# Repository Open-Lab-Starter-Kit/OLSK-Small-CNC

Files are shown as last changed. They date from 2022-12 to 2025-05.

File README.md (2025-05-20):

<div align="center"><h1 style=align="center">OLSK Small CNC V3</h1></div>

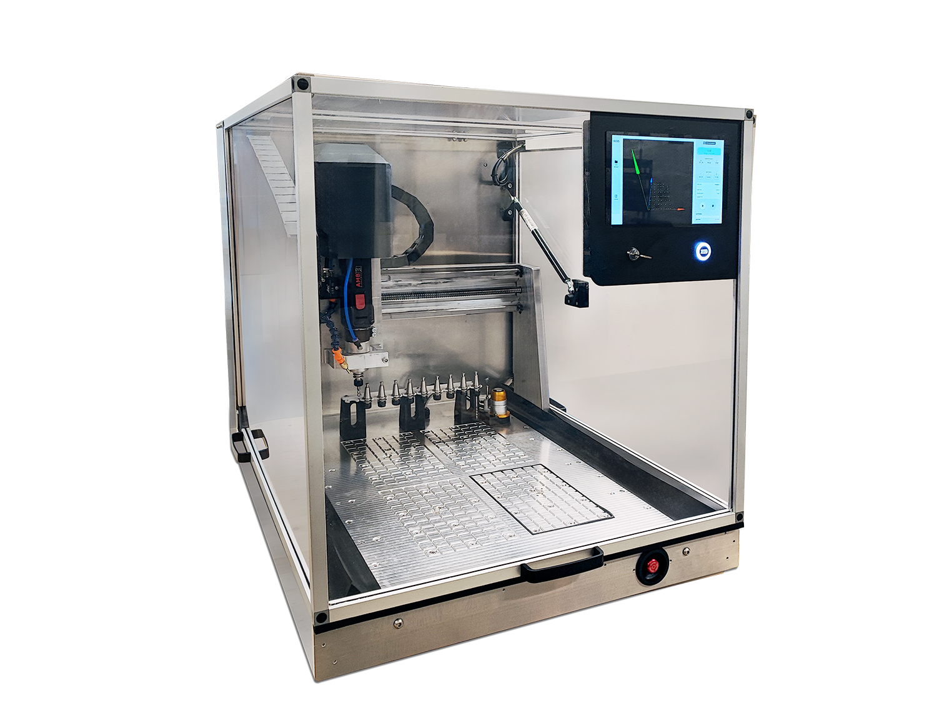
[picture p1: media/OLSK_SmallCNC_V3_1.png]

<div align="center"><i>Open Source CNC Milling machine - Small version - Open Lab Starter Kit</i></div>

<br>

Introduction
--

The OLSK Small CNC V3 is a desktop CNC milling machine with an innovative open-source tool changer, one of the first in an open-source machine.



The Assembly Manual
--

All OLSK machines are open source and have the BOM and necessary files available in this repository for replication. The assembly of parts is also documented in a workbook where each step contains a list of parts, tools and instruction remarks, following a logical order to provide a smooth assembly.

- **[Assembly Manual](https://open-lab-starter-kit.github.io/OLSK-Small-CNC/)**

Specifications V3
--

- machine external dimensions: W740mm x D960mm x H800mm (~H1600mm open door)
- working area: 400mm x 600mm x 150mm Width(X) x Depth(Y) x Height(Z)
- Automatic tool changer (capacity: 10 tools)
- Automatic tool measurement
- Automatic tool cleaning
- Coolant System
- Integrated liftable full-enclosed housing
- Flush-mounted 24V emergency stop
- Key Operated
- Universal bed (fixture clamping and vacuum)
- Closed Loop DC Servo Motors
- Belt decoupling on all axes
- Mounted touch screen
- Software: OLOS

Files
--

- **[CAD](cad)**
- **[Firmware](firmware)**
- **[Settings](settings)**
- **[BOM](OLSK_Small_CNC_V3-BOM.xlsx)**
- **[Wiring Schematic](OLSK_Small_CNC_V3_WiringSchematic.pdf)**

Author
--

OLSK Small CNC has been designed and built by **[InMachines Ingrassia GmbH](https://www.inmachines.net/)**.



<be>

Machine design:
- **[Daniele Ingrassia](https://www.linkedin.com/in/danieleingrassia/)**

PCB Design:
- **[Wilhelm Schütze](http://fabacademy.org/archives/2015/sa/students/schutze.wilhelm/index.html)**

The machine is part of the **[Open Lab Starter Kit (OLSK)](https://www.inmachines.net/open-lab-starter-kit)** group of open source digital fabrication machines.

OLSK is developed by **[InMachines Ingrassia GmbH](https://www.inmachines.net/)** for the **[Dtec project](https://dtecbw.de/home/forschung/hsu/projekt-fabcity)** at **[Fab City Hamburg](https://www.fabcity.hamburg/en/)**.

OLSK Partners:
<br><br>


Contact
--

- daniele@inmachines.net
- [https://www.inmachines.net/](https://www.inmachines.net/)

License
--

Hardware design, CAD and PCB files, BOM, settings and other technical or design files are released under the following license:

- CERN Open Hardware Licence Version 2 Weakly Reciprocal - **[CERN-OHL-W](LICENSE_CERN_OHL_W_V2.txt)**

Assembly manual, pictures, videos, presentations, description text and other type of media are released under the following license:

- Creative-Commons-Attribution-ShareAlike 4.0 International - **[CC BY-SA 4.0](LICENSE_CC_BY_SA_4.0.txt)**

Copyright
--

- Daniele Ingrassia, InMachines Ingrassia GmbH

- Tobias Redlich, Helmut-Schmidt-Universität/Universität der Bundeswehr Hamburg

Previous Version
--

The previous versions of OLSK machines will always be available.

**[OLSK Small CNC Milling Machine V2](OLSK_Small_CNC_V1)**
<br> <br>
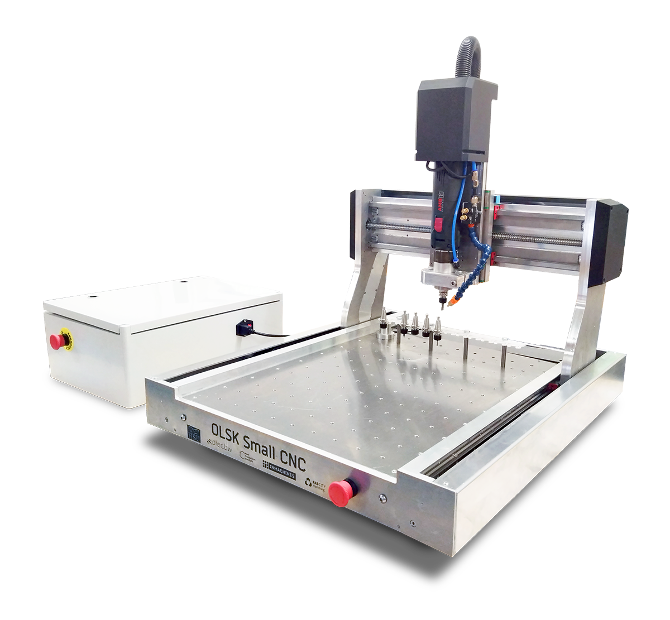
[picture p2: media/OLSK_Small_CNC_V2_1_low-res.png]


**[OLSK Small CNC Milling Machine V1](OLSK_Small_CNC_V1)**
<br> <br>
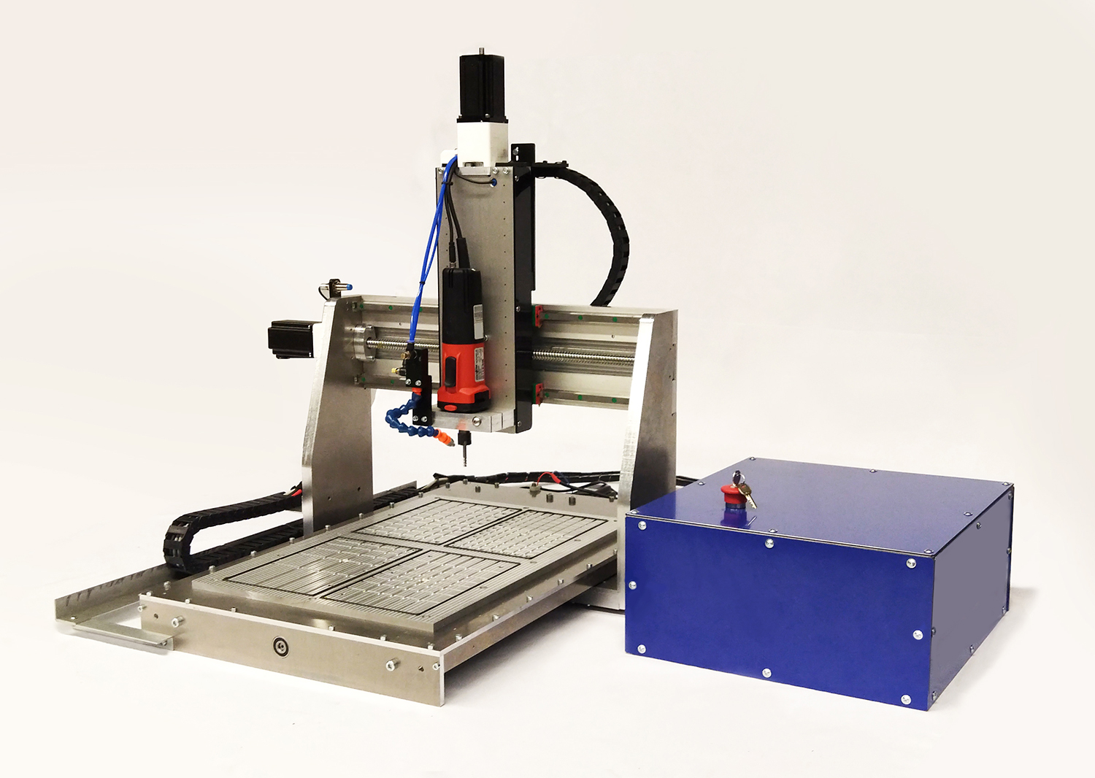
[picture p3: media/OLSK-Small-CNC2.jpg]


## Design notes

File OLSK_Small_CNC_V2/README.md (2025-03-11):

<div align="center"><h1 style=align="center">OLSK Small CNC V2</h1></div>


<div align="center"><i>Open Source CNC Milling machine - Small version - Open Lab Starter Kit</i></div>

<br>

Introduction
--

The OLSK Small CNC V2 is a desktop CNC milling machine with an innovative open-source tool changer, one of the first in an open-source machine. Its compact and sturdy design with aluminum frame has a milling volume of 400 x 500 x 140 mm (X x Y x Z). The Z-axis is compact, with a minimum distance to the X-axis linear guides, giving the milling more stability and sturdiness. The machine also includes a Z height tool sensor and homing with inductive sensors.

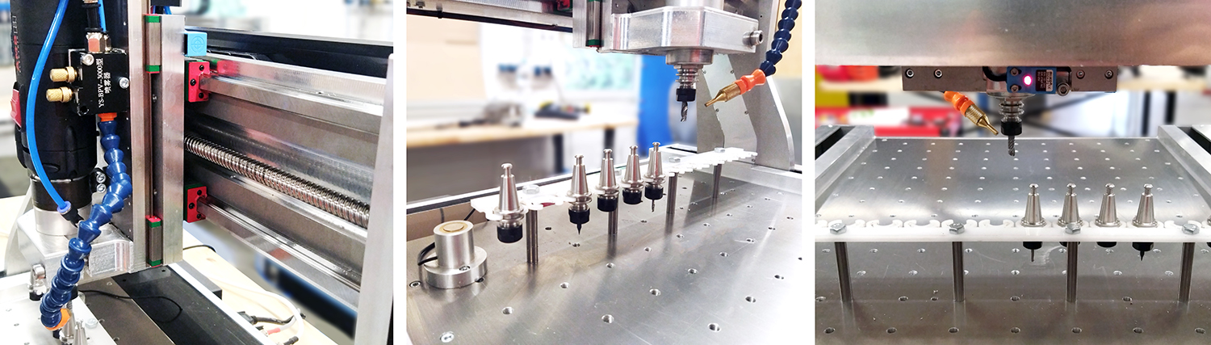
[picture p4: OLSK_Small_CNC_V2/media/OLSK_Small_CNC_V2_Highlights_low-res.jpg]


The Assembly Workbook
--

All OLSK machines are open source and have the BOM and necessary files available in this repository for replication. The assembly of parts is also documented in a workbook where each step contains a list of parts, tools and instruction remarks, following a logic order to provide a smooth assembly.

Specifications V1
--

- milling volume: 400 x 500 x 140 mm
- frame: solid aluminum
- bed: CNC milled aluminum
- firmware: Grbl Hal
- additional: tool changer, coolant system
- Z height tool sensor

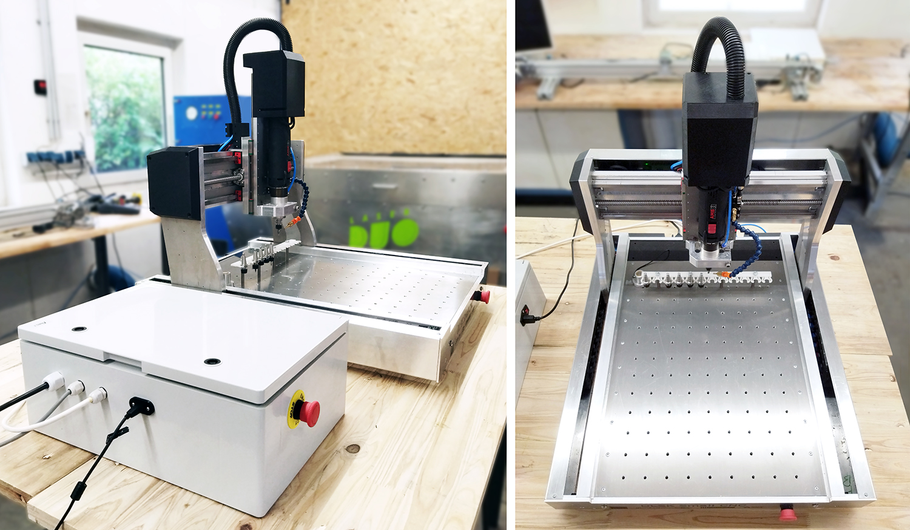
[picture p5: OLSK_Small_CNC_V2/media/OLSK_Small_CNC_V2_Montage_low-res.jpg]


Files
--

- **[Assembly Workbook](OLSK_Small_CNC_V2_Workbook.pdf)**
- **[CAD](CAD)**
- **[Firmware](Firmware)**
- **[PCB](https://github.com/Open-Lab-Starter-Kit/OLSK-Electronics/tree/main/Laser_CNC_Board_V3-5)**
- **[Wiring Schematic](OLSK_Small_CNC_V2_Wiring.pdf)**
  
Author
--

OLSK Small CNC has been designed and built by **[InMachines Ingrassia GmbH](https://www.inmachines.net/)**.



<be>

Machine main body design:
- **[Rahul S. Rajan](https://www.linkedin.com/in/rahulsrajan/?originalSubdomain=de)**

Automatic Tool Changer design:
- **[Daniele Ingrassia](https://www.linkedin.com/in/danieleingrassia/)**

PCB Design: 
- **[Wilhelm Schütze](http://fabacademy.org/archives/2015/sa/students/schutze.wilhelm/index.html)**

The machine is part of the **[Open Lab Starter Kit (OLSK)](https://www.inmachines.net/open-lab-starter-kit)** group of open source digital fabrication machines.

OLSK is developed by **[InMachines Ingrassia GmbH](https://www.inmachines.net/)** for the **[Dtec project](https://dtecbw.de/home/forschung/hsu/projekt-fabcity)** at **[Fab City Hamburg](https://www.fabcity.hamburg/en/)**.

OLSK Partners:
<br><br>


Contact
--

- daniele@inmachines.net
- [https://www.inmachines.net/](https://www.inmachines.net/)

License
--

Hardware design, CAD and PCB files, BOM, settings and other technical or design files are released under the following license:

- CERN Open Hardware Licence Version 2 Weakly Reciprocal - **[CERN-OHL-W](LICENSE_CERN_OHL_W_V2.txt)**

Assembly manual, pictures, videos, presentations, description text and other type of media are released under the following license:

- Creative-Commons-Attribution-ShareAlike 4.0 International - **[CC BY-SA 4.0](LICENSE_CC_BY_SA_4.0.txt)**

Previous Version
--

**[OLSK Small CNC Milling Machine V1](OLSK_Small_CNC_V1)**
<br> <br>


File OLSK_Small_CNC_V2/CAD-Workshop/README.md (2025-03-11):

Here the CAD file for the Small CNC workshop @ Motion Lab Berlin 7th-9th October.

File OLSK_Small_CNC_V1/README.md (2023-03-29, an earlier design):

<div align="center"><h1 style=align="center">OLSK Small CNC V1</h1></div>

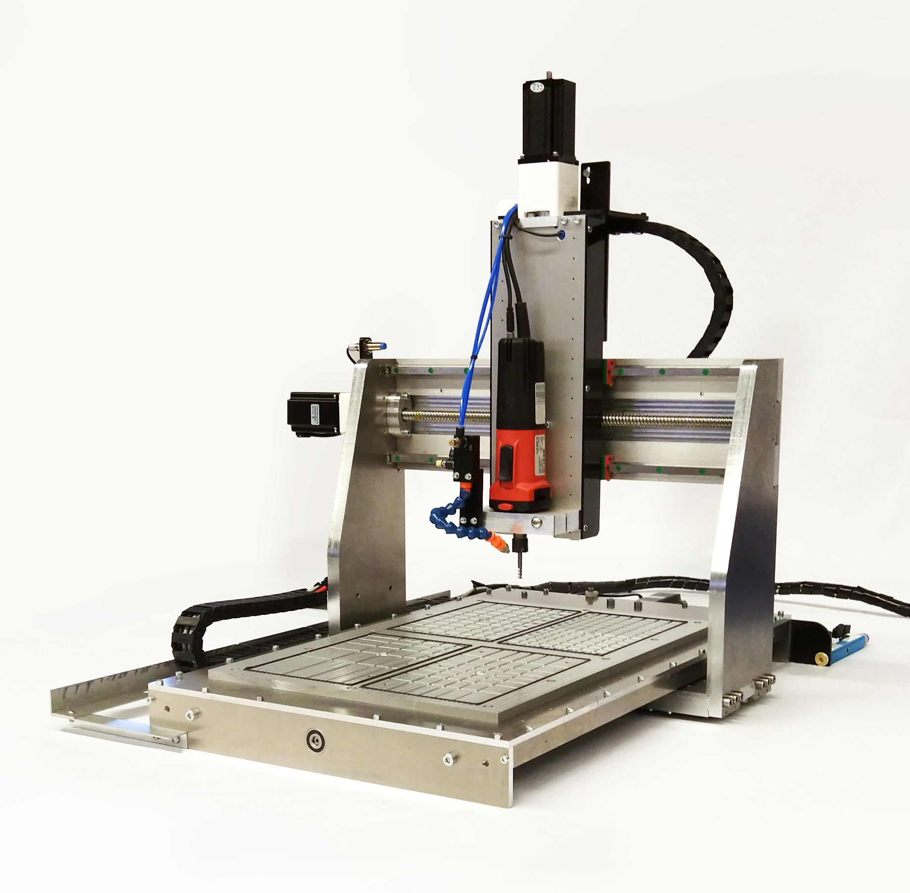
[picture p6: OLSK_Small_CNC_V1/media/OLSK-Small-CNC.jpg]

<div align="center"><i>Open Source CNC Milling machine - Small version - Open Lab Starter Kit</i></div>

<br>

Introduction
--

The OLSK Small CNC V1 is a desktop CNC milling machine with innovative, compact and sturdy design. The bed, with a milling volume of 600 x 400 x 170 mm (X x Y x Z), features a powerful vacuum system to hold plates without clamping. It is also adapted to fit different international unit systems to allow the fixation of different vices and other accessories. The Z-axis is compact, with a minimum distance to the X-axis linear guides, giving the milling more stability and sturdiness. The linear guides from the Y and Z axis are protected against material chips. The machine also includes a Z height tool sensor and homing with inductive sensors.

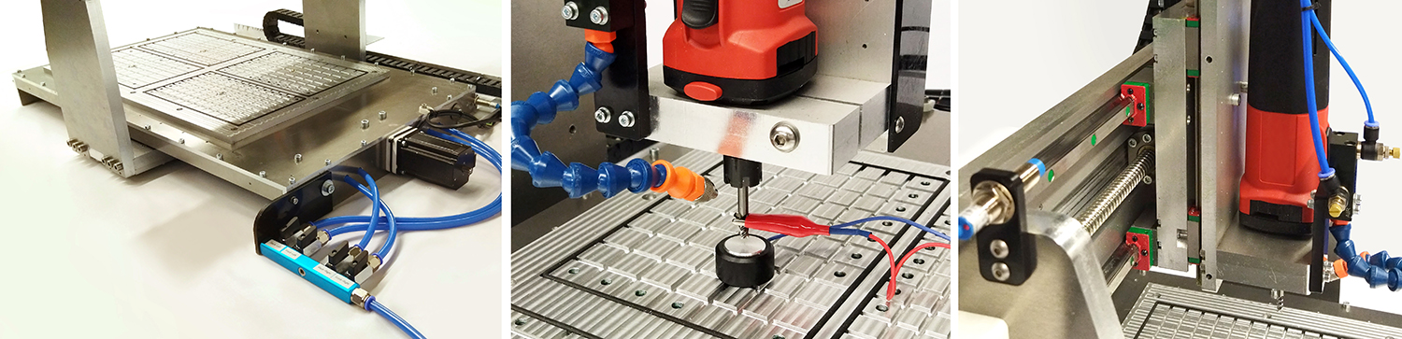
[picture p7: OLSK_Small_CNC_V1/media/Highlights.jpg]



Learning by Making
--

The OLSK Small CNC V1 can be offered as an assembly kit with all the necessary parts to build it, saving the user the time to produce and procure the parts. Building a machine provided the opportunity to understand how the machine operates from the inside and the function of each part. This machine can also be built with the help of a workshop lead by the InMachines team, as unique learning experience for small groups, resulting in a full operational CNC milling machine for your makerspace.

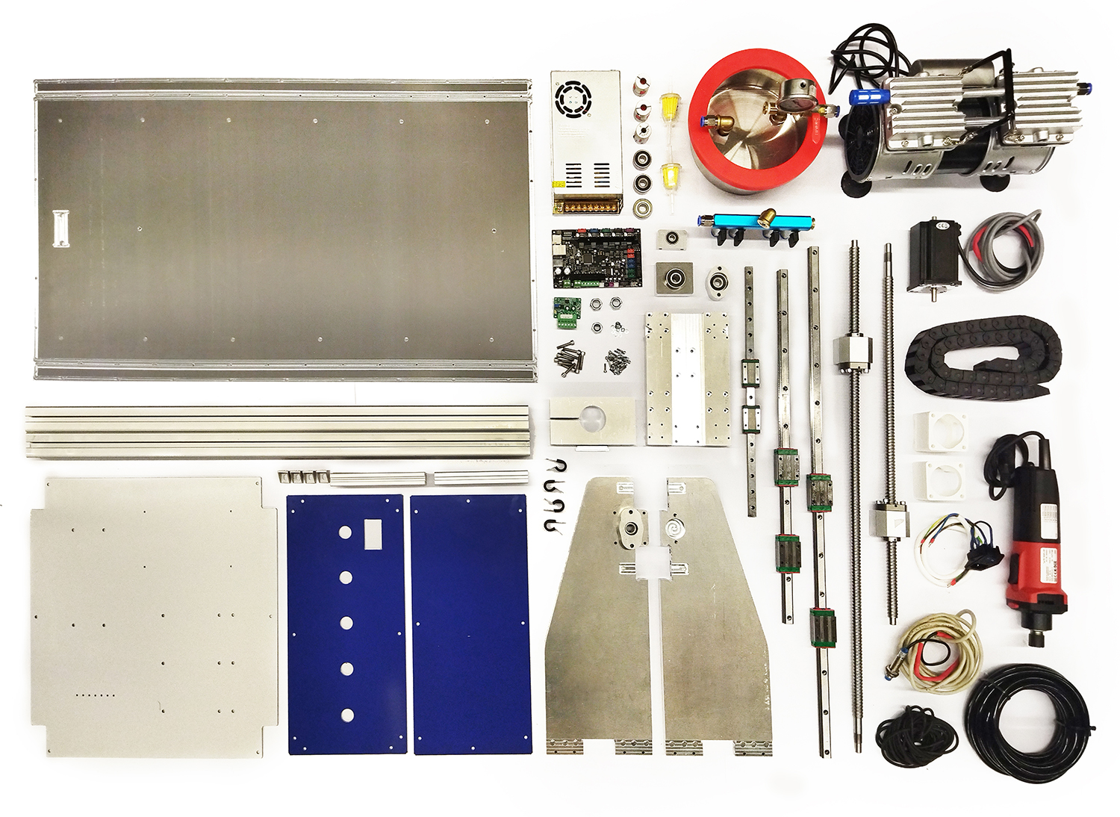
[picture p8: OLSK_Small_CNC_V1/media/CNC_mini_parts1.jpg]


The Assembly Workbook
--

All OLSK machines are open source and have the BOM and necessary files available in this repository for replication. The assembly of parts is also documented in a workbook where each step contains a list of parts, tools and instruction remarks, following a logic order to provide a smooth assembly.

Specifications V1
--

- milling volume: 600 x 400 x 170 mm
- frame: solid aluminum
- electronic box frame: 20 x 2m mm aluminum profiles
- electronic box housing: aluminum composite
- bed: CNC milled aluminum
- motion: ball screws 12 and 16 mm
- guides: 15 mm linear rails
- motors: stepper motor NEMA 24
- firmware: grbl-LPC
- additional: modular vacuum bed and coolant system
- Z height tool sensor
- bed compatible with different international unit systems

Files
--

- **[Assembly Workbook](OLSK_Small_CNC_V1_Workbook.pdf)**
- **[Wiring Schematic](OLSK_Small_CNC_V1_Wiring_Schematic.pdf)**
- **[BOM](OLSK_Small_CNC_V1_BOM.pdf)**
- **[CAD](cad)**
- **[Firmware](firmware)**
- **[Sensor PCB](ProbeConverter-Triple)**
- **[Fusion 360 machine settings](machine_settings)**
- **[Z tool Sensor detection](Z_Tool_Probe.nc)**

Author
--

OLSK Small CNC has been designed and built by **[InMachines Ingrassia GmbH](https://www.inmachines.net/)**.



<br>

Machine design:
- **[Daniele Ingrassia](https://www.linkedin.com/in/danieleingrassia/)**

The machine is part of the **[Open Lab Starter Kit (OLSK)](https://www.inmachines.net/open-lab-starter-kit)** group of open source digital fabrication machines.

OLSK is developed by **[InMachines Ingrassia GmbH](https://www.inmachines.net/)** for the **[Dtec project](https://dtecbw.de/home/forschung/hsu/projekt-fabcity)** at **[Fab City Hamburg](https://www.fabcity.hamburg/en/)**.

OLSK Partners:
<br><br>


Contact
--

- daniele@inmachines.net
- [https://www.inmachines.net/](https://www.inmachines.net/)

License
--

Hardware design, CAD and PCB files, BOM, settings and other technical or design files are released under the following license:

- CERN Open Hardware Licence Version 2 Weakly Reciprocal - **[CERN-OHL-W](LICENSE_CERN_OHL_W_V2.txt)**

Assembly manual, pictures, videos, presentations, description text and other type of media are released under the following license:

- Creative-Commons-Attribution-ShareAlike 4.0 International - **[CC BY-SA 4.0](LICENSE_CC_BY_SA_4.0.txt)**

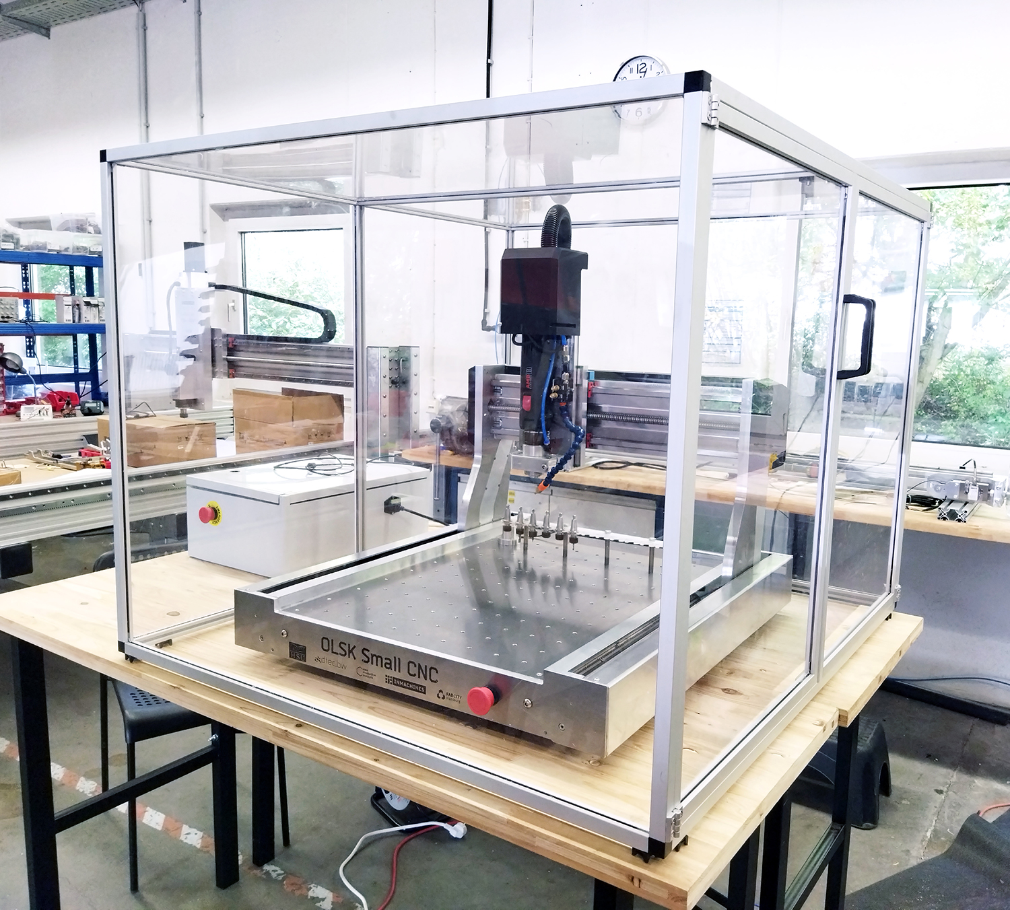
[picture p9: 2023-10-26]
OLSK_Small_CNC_V2/media/OLSK_Small_CNC_V2_Detail2_low-res.jpg

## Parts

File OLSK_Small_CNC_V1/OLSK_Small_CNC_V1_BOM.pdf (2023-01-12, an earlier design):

Ready made parts

Accessories
Production Name | Specifications | Amount | Current Price | Total | Shipping | Vendor | Label Name | Checks / ToDo | Notes
Vacuum Pump (optional) | Double Piston Vacuum Pump RS 550 A Oil-Free Vacuum Pump | 1 | €200.00 | €200.00 | €0.00 | link (https://www.amazon.de/gp/product/B078ND2SPY/ref=ppx_yo_dt_b_asin_title_o06_s00?ie=UTF8&th=1)
Air Compressor | Airbrush AS-48A or equivalent | 1 | €180.00 | €180.00 | €0.00 | link (https://www.amazon.de/-/en/Pro-Lift-Werkzeuge-Airbrush-Compressor-Cylinder-Automatic/dp/B088KD5Q83?s=diy)
Coolant System (optional) | BZT Minimalmengenschmierung MDM | 1 | €213.00 | €213.00 | €0.00 | link (https://www.ebay.de/itm/392121599819) | | | includes air and coolant pipes
Foot Switch | 240V Eco Line Comfort Switch Adapter | 1 | €11.13 | €11.13 | €2.99 | link (https://www.ebay.de/itm/BRENNENSTUHL-Eco-Line-Comfort-Switch-Adapter/233743985229?epid=22011384030)

Radial Fan (optional)
Vacuum Chamber (optional) | 1.2 with valve and connectors | 1 | €42.00 | €42.00 | €0.00 | link (https://www.ebay.de/itm/115130524707) | | | needs to be drille with an output
Vacuum Filter (optional) | Universal gas (benzin) filter 6/8mm | 1 | €3.00 | €5.00 | €0.00 | link (https://www.ebay.de/itm/302862502448)
Dot Sticker | | 2
Cable Tie | | 1
Teflon Tape | | 1

Air Valve Label
Linear Guide Cap | | 20

Safety Stickers

Rubber Cord

Electrics Electronics
Production Name | Specifications | Amount | Current Price | Total | Shipping | Vendor | Label Name | Checks / ToDo | Notes
Router | Mafell 9M0401 milling motor FM 1000 PV ER | 1 | €250.00 | €250.00 | €0.00 | link (https://www.amazon.de/gp/product/B08BJ177CW/ref=ppx_yo_dt_b_asin_title_o09_s00?ie=UTF8&psc=1) | | Cable needs to be extended | alternative a manual spindel can be used
Power Supply | 24V 20A LED form factor DM556T | 1 3 | €33.00 €28.00 | €33.00 €84.00 | €0.00 | link (https://www.amazon.de/gp/product/B0896Z8Y3D/ref=ppx_yo_dt_b_asin_title_o01_s00?ie=UTF8&psc=1) | | Test Motor Driver
| Dual Shaft Nema 24 Stepper Motor 4.2A 4Nm 24HS39-4204D | 3 | €40.00 | €120.00 | €8.00 | link (https://www.omc-stepperonline.com/digital-stepper-driver-18~56a-20-50vdc-for-nema-23-24-34-stepper-motor-dm556t.html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) link | Cables need to be extended Test Motor
USB Cable Inside | Panel mount USB B | 1 | €2.59 | €2.59 | €2.49 | link (https://www.ebay.de/itm/USB-2-0-B-Stecker-auf-USB-B-Buchse-Einbau-Panel-mount-gewinkelt-50cm-3D-Drucker/174056486363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)
USB Cable | 3m shielded, 90 connector | 1 | €2.19 | €2.19 | €0.00 | link (https://www.ebay.de/itm/3-m-USB-2-0-Hi-Speed-Kabel-USB-Stecker-A-B-Winkelstecker-90-Unten-5611/280965602663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)
Power Cable | PC Power Cable | 1 | €4.50 | €4.50 | €0.00 | link (https://www.ebay.de/itm/Manhattan-Powerkabel-Stromkabel-PC-Drucker-Monitor-Fernseher-1-5m-Schwarz/253379816568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)
Fuse | 6.3A 5x20mm | 2 | €0.29 | €0.57 | €0.00 | link (https://www.ebay.de/itm/10x-Glassicherung-F-6-3-A-Flink-5x20mm-FSP-Sicherung-6300-mA-Feinsicherung-time/264578536585)
Y-chain | Cable Chain 15x30mm 1 meter | 2 | €13.74 | | | link (https://gtech-shop.de/Schleppkette-Energiekette-1530mm-Innenmasse-R28)
X-chain | Cable Chain 10x20mm 1 meter | 2 | €12.09 | | | link (https://gtech-shop.de/Schleppkette-Energiekette-1020mm-Innenmasse-R28)
Controller PCB | Teensy 4.1 + Our custom shield | 1
Router PCB | Digital Analog Converter - 3.3V PWM Signal to 0-10V Voltage Converter D/A Digital Analog PLC Module | 1
Relay | Arduino Relay module blue | 1
Cable Gland | M20 | 5
Relay Jumper M-M | | 1
Cable Connector | | 1
Emergency Button | same as Fabulaser with Key | 1
Cable Wrapper Bottom | | 1
Cable Wrapper Top | | 1

Air/Hydraulics

Production Name | Specifications | Amount | Current Price | Total | Shipping | Vendor | Label Name | Checks / ToDo | Notes
Air Valve | Mini Ball Valve Size 1/4 Inch Inner x External Thread (female-male) | 4 | €6.50 | €26.00 | €0.00 | link (https://www.amazon.de/gp/product/B00D0QWSLU/ref=ppx_yo_dt_b_asin_title_o05_s00?ie=UTF8&psc=1)
Air Splitter | 5 Way Splitter 1/4 | 1 | €15.00 | €15.00 | €0.00 | link (https://www.amazon.de/gp/product/B099DWPJQ4/ref=ppx_yo_dt_b_asin_title_o08_s01?ie=UTF8&psc=1)
Fit Connector | Straight male connector, quick connector, push in 1/4 x 10mm | 10 | €1.76 | €17.60 | €0.00 | link (https://www.amazon.de/gp/product/B0108HHGSI/ref=ppx_yo_dt_b_asin_title_o06_s00?ie=UTF8&th=1)
Angle Air Connector | 90 angled male connector, quick connector, push in 1/4 x 10mm | 1
Air Tube | Outder diamter 10mm 6 meters | 1 | €17.00 | €17.00 | €0.00 | link (https://www.amazon.de/gp/product/B07THHX3Q5/ref=ppx_yo_dt_b_asin_title_o08_s03?ie=UTF8&psc=1)
Inductive Sensor | Inductive Probe LJ12A3-4-Z/AY | 3 | €6.00 | €18.00 | €3.00 | link (https://www.ebay.de/itm/123250430545)
Angle Connector | G 1/4 90 degree compact female-male connector | 4 | €5.00 | €20.00 | €0.00 | link (https://www.amazon.de/gp/product/B0771M7DKN/ref=ppx_yo_dt_b_asin_title_o08_s00?ie=UTF8&psc=1)
Air Cap | G 1/4 Brass socket screw male cap | 4 | €1.10 | €4.40 | €2.90 | link (https://www.ebay.de/itm/152614986705?var=452073737236)

Coolant pipes (optional)

O Ring | 5 | Mechanics
Production Name | Specifications | Amount | Current Price | Total | Shipping | Vendor | Label Name | Checks / ToDo | Notes
Ball screw Z | 1204 300mm with Nut | 1 | €52.00 | €52.00 | €6.90 | link (https://www.dold-mechatronik.de/Ball-spindle-1204-3-with-nut-length-300mm)
Ball screw X | 1610-3 600mm with Nut | 1 | €70.00 | €70.00 | | link (https://www.dold-mechatronik.de/Ball-spindle-1610-3-with-nut-length-600mm)
Ball screw Y | 1610-3 800mm with Nut | 1 | €76.00 | €76.00 | | link (https://www.dold-mechatronik.de/Ball-spindle-1610-3-with-nut-length-800mm)
Linear Guide Z | MGN12 400mm with 2 carriages type MGN12H (large one) | 2 | €50.00 | €100.00 | €0.00 | link (https://www.amazon.de/-/en/Appliances-Automatic-Equipment-Precision-Measuring/dp/B08S3F8BRC?rnid=15431285031) | | | about price
Linear Guide X | HGR15RC 560mm | 2 | €30.60 | €61.20 | €25.00 | link (https://www.cnc-store.eu/componenti-meccanici/guide-a-ricircolo/guide/guida-hiwin-hgr15-r-c.html)
Linear Guide Y | HGR15RC 800mm | 2 | €40.80 | €81.60 | | link (https://www.cnc-store.eu/componenti-meccanici/guide-a-ricircolo/guide/guida-hiwin-hgr15-r-c.html)
Carriage | HGH15CAZA C | 8 | €25.01 | €200.08 | | link (https://www.cnc-store.eu/componenti-meccanici/guide-a-ricircolo/cursori/cursore-hgh15caza-c.html)
Screw Block Z | Ball Screw attachment block DSG12 for 1204 | 1 | €8.00 | €8.00 | | link

Screw Block XY | Ball Screw attachment block DSG16 for 1610 | 2 | €8.00 | €16.00 | €7.00 | link
Profile 40 | Aluminum Profile 40x40 Nut 8 800mm | 2 | €13.50 | €27.00

€10.00

link (https://www.ebay.de/itm/261818937804?hash=item3cf59ff1cc:g:6YYAAOSwb19h79Zn)
Profile 20-400 | Aluminum Profile 20x20 Nut 6 400mm | 8 | €2.50 | €20.00 | link (https://www.ebay.de/itm/262637440058?hash=item3d26694c3a:g:WY8AAOSwuYth78x5)
Profile 20-150 | Aluminum Profile 20x20 Nut 5/6 150mm | 4 | €1.50 | €6.00 | link (https://www.ebay.de/itm/262637440058?hash=item3d26694c3a:g:WY8AAOSwuYth78x5)
Brackets | Bracket 20x20 Nut 5 | 24 | €11.00 | €11.00 | €0.00 | link (https://www.amazon.de/-/en/LYTIVAGEN-Aluminium-Connector-Structure-Construction/dp/B07L871GY1)
Z Bottom Bearing | Angular Ball Bearing 30/8 2RS TN 8x22x11 mm | 1 | €5.30 | €5.30 | €5.00 | link (https://www.kugellager-express.de/angular-ball-bearing-30-8-2rs-tn-8x22x11-mm)
Z Top Bearing | Angular Ball Bearing 3000 2RS TN 10x26x12 mm | 1 | €5.70 | €5.70 | link (https://www.kugellager-express.de/angular-ball-bearing-3000-2rs-tn-10x26x12-mm)

X Right Bearing
Y Front Bearing | 5200 2RS TN / 3200 2RS TN 10x30x14 mm | 2 | €6.30 | €12.60 | link (https://www.kugellager-express.de/angular-ball-bearing-5200-w14-2rs-tn-3200-w14-2rs-tn-10x30x14-mm)

X Back Bearing
Y Back Bearing | Angular Ball Bearing 5201 2RS TN / 3201 2RS TN 12x32x15.9 mm | 2 | €7.00 | €14.00 | link (https://www.kugellager-express.de/angular-ball-bearing-5201-2rs-tn-3201-2rs-tn-12x32x15-9-mm)
Supporting Bearing | Deep Groove Ball Bearing 6201 2RS 12x32x10 mm | 2 | €1.30 | €2.60 | link (https://www.kugellager-express.de/deep-groove-ball-bearing-6201-2rs-12x32x10-mm)
Coupler Z | Coupler D25L30 8mm to 8mm | 1
Coupler XY | Coupler D25L30 8mm to 10mm | 2 | Manufactured Parts
Production Name | Specifications | Amount | Current Price | Total | Shipping | Vendor | Label Name | Checks / ToDo | Notes Motor Driver Logic Cable | 3 core 40 cm + F jumpers + 2x M jumper | 3
Sensor Logic Cable | 4 core 35 cm + F jumpers 45 cm | 1 Motor Driver Power Cable 3
Controller PCB Power Cable | 60 cm | 1
Sensor PCB Power Cable | 35 cm | 1
Router PCB Power Cable | Mafell control cable | 1
Emergency Button Cable | 55 cm | 1
Power Plug + Mains Cable | Mains 55 cm | 1
Earth Cable Inside + Earth Cable Outside | Earth Inside 23 cm, Earth outside 100 cm | 1
Relay Jumper F-F | One must be extended | 3
X-endstop sensor | 280 cm | 1
Y-endstop sensor | 110 cm | 1
Z-endstop sensor | 360 cm | 1
Z-height sensor | 257 cm | 1
Router Cable | 400 cm | 1
Z-motor | 410 cm | 1
Y-motor | 225 cm | 1
X-motor | 280 cm | 1
X-chain Bottom Support | Aluminum bracket 40x30 550mm | 1
Y-chain Top Support | Aluminum bracket 70x30 168mm | 1
Y-chain Bottom Support Front | Aluminum bracket 30x20 190mm | 1
Y-chain Bottom Support Back | Aluminum bracket 30x20 190mm
Y-chain Bottom Support Side | Aluminum bracket 40x30 885mm | 1
Router PCB Jumper | | 1
Router Control Cable | 1 | Milled Parts
Box Bottom Panel | | 1
Box Left Panel | | 1
Box Back Panel | | 1
Box Right Panel | | 1
Box Front Panel | | 1
Box Top Panel | | 1
Base Plate | | 1
Base side protection | | 2
Base Front | with prefixed Y Front Bearing | 1
Base Back | | 1
Bed | | 1
Y Back Bearing Holder | with prefixed Y Back Bearing | 1
Shoulder Support Left | | 1
Shoulder Support Right | | 1

Y Connector Plate | | 1
X Plate | | 1
Left Shoulder | With bearing holder and bearings(5201&6201) + two screws pre-attached. | 1
Right Shoulder | | 1
X Bearing Holder Right | With X Right Bearing prefit | 1

X Bearing Holder Left

Z Front Plate | | 1
Z Top Plate | | 1
Z bottom bearing Holder | With Z Bottom Bearing prefix | 1
Z Top Bearing Cover | | 1 Middle Plate 1
Router Holder | | 1
Sensor PCB | | 1
| | 1 Wire Fixer Big 1 | 3D Printed Parts Wire Fixer Small
Z-motor Adapter | | 1
X-motor Adapter | | 1
Y-motor Adapter | | 1
Z Sensor Holder | to be added for an easier attachment of the Z Sensor | 1

Laser Cutted Parts

Coolant System Holder | 1
Air Splitter Holder | 1
Z-screw Holder | 1
Screw Holder Spacer | 5
X-chain Top Support | 1
X-endstop Sensor Holder | 1
Y-endstop Sensor Holder | 1
Z Side Panel Right | 1
Z Side Panel Left | 1
Fasteners Manual name | Specifications | Amount | Current Price | Total | Shipping | Vendor | Label Name | Checks / ToDo | Notes
Hammer Nut M5 | Hammer Nut 6 M5 Rotation | 81
C-screw M3-12 | DIN 912 M3 12mm | 56
C-screw M3-25 | DIN 912 M3 25mm | 16
C-screw M4-8 | DIN 912 M4 8mm | 4 | about price
C-screw M4-12 | DIN 912 M4 12mm | 6
C-screw M4-16 | DIN 912 M4 16mm | 35
C-screw M4-25 | DIN 912 M4 25mm | 14
C-screw M4-30 | DIN 912 M4 30mm | 16
C-screw M4-35 | DIN 912 M4 35mm | 2
C-screw M5-8 | DIN 912 M5 8mm | 16
C-screw M5-10 | DIN 912 M5 10mm | 2
C-screw M5-16 | DIN 912 M5 16mm | 20
C-screw M5-20 | DIN 912 M5 20mm | 48
C-screw M5-25 | DIN 912 M5 25mm | 12
C-screw M5-35 | DIN 912 M5 35mm | 8
C-screw M5-70 | DIN 912 M5 70mm | 4
C-screw M5-80 | DIN 912 M5 80mm | 4
C-screw M6-12 | DIN 912 M6 12mm | 3
C-screw M6-16 | DIN 912 M6 16mm | 4
C-screw M6-25 | DIN 912 M6 25mm | 11
C-screw M6-35 | DIN 912 M6 35mm | 8
C-screw M8-25 | DIN 912 M8 25mm | 4
C-screw M8-30 | DIN 912 M8 30mm | 2
C-screw M8-35 | DIN 912 M8 35mm | 16
C-screw M8-40 | DIN 912 M8 40mm | 12
C-screw M8-70 | DIN 912 M8 70mm | 1
B-screw M5-8 | ISO 7380-2 M5 8mm | 6
B-screw M5-12 | ISO 7380-2 M5 12mm | 9
B-screw M5-20 | ISO 7380-2 M5 20mm | 8

B-screw M6-16 | ISO 7380-2 M6 16mm | 5
B-screw M6-20 | ISO 7380-2 M6 20mm | 10
B-screw M6-30 | ISO 7380-2 M6 30mm | 1
B-screw M8-12 | ISO 7380-2 M8 12mm | 2
Hexagon Screw M6-12 | DIN 933 M6 12mm | 1
Lock Nut M3 | DIN 985 M3 | 4
Lock Nut M4 | DIN 985 M4 | 6
Lock Nut M5 | DIN 985 M5 | 11
Lock Nut M6 | DIN 985 M6 | 5
Standoff | Plastic Spacer M3 15mm | 10
Plastic Screw M3-8 | Plastic Screw M3 8mm DIN7985 or similar | 12 Washer M3 | DIN 125 M3 | 4 Washer M4 | DIN 125 M4 | 8 Washer M5 | DIN 125 M5 | 15 Washer M6 | DIN 125 M6 | 5 Washer M8 | DIN 125 M8 | 1 Washer M10 | DIN 125 M10 | 4 Washer M12 | DIN 125 M2 | 4 Washer M8 Big | DIN 9021 M8 | 1
Locknut M10 Pitch 1 mm | DIN 985 Fine pitch 1mm | 1
Locknut M12 Pitch 1 mm | DIN 985 Fine pitch 1mm | 2
T-nut 8 M6 | | 12
Flat screw | | 3

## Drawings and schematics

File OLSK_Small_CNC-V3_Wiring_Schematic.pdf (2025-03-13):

# OLSK SMALL CNC V3

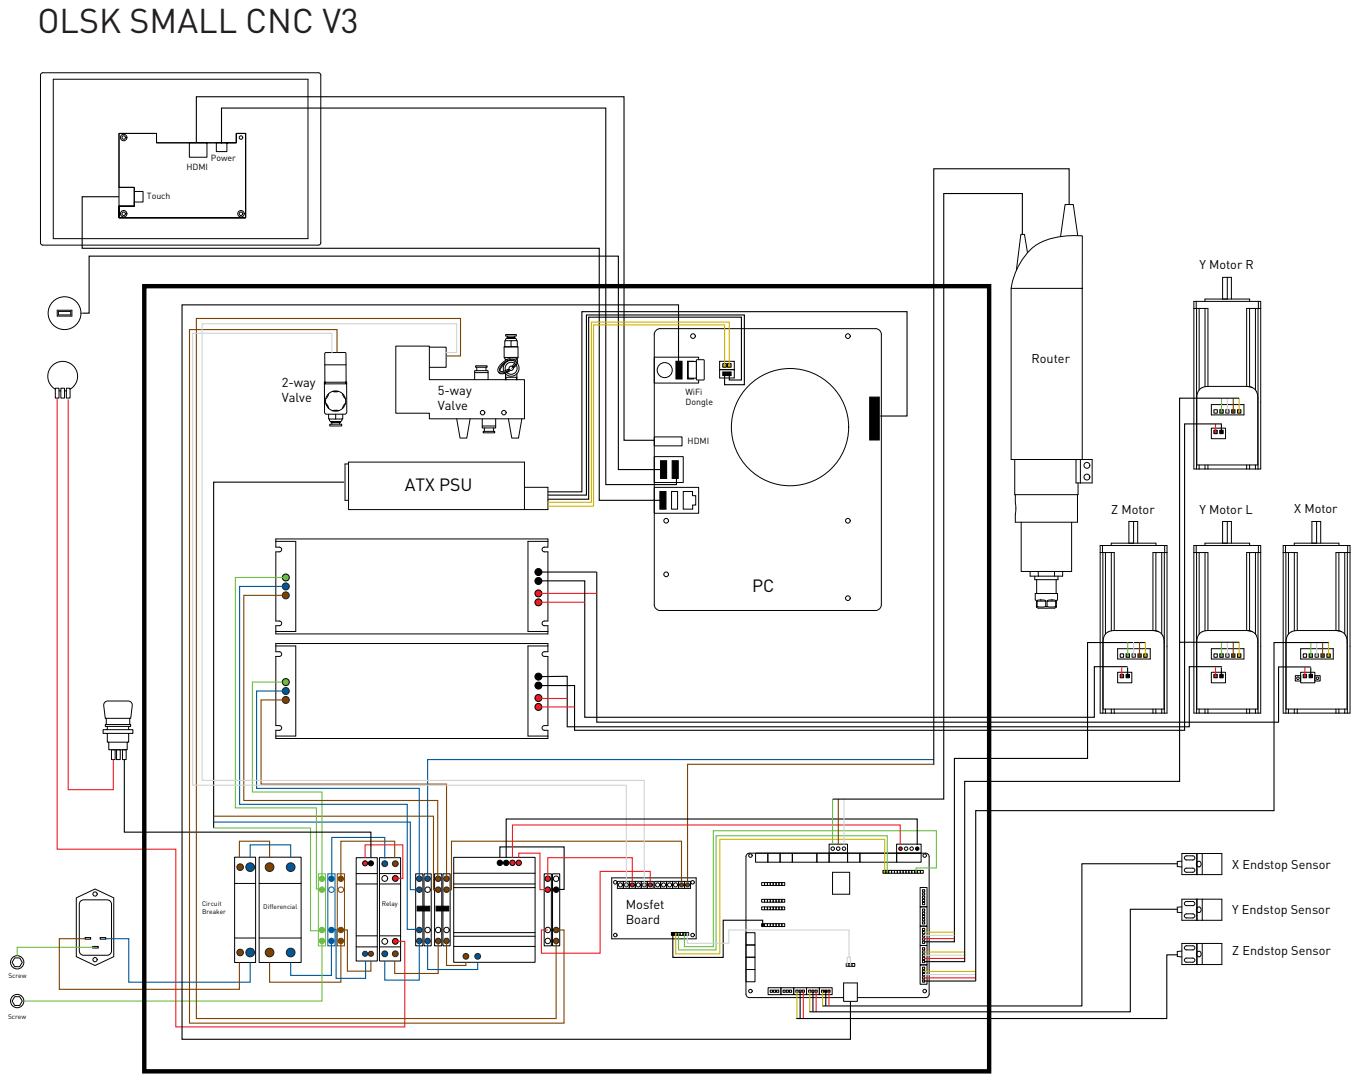
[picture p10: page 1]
Router; X Endstop Sensor; Z Motor; Y Motor L; X Motor; Y Motor R; Y Endstop Sensor; Z Endstop Sensor; HDMI; WiFi Dongle; Touch; Power; ATX PSU; 2-way; Valve; 5-way; Mosfet Board; Circuit Breaker; Relay; Screw; Differencial

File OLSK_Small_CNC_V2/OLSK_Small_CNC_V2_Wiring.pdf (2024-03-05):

# Z Endstop

Z

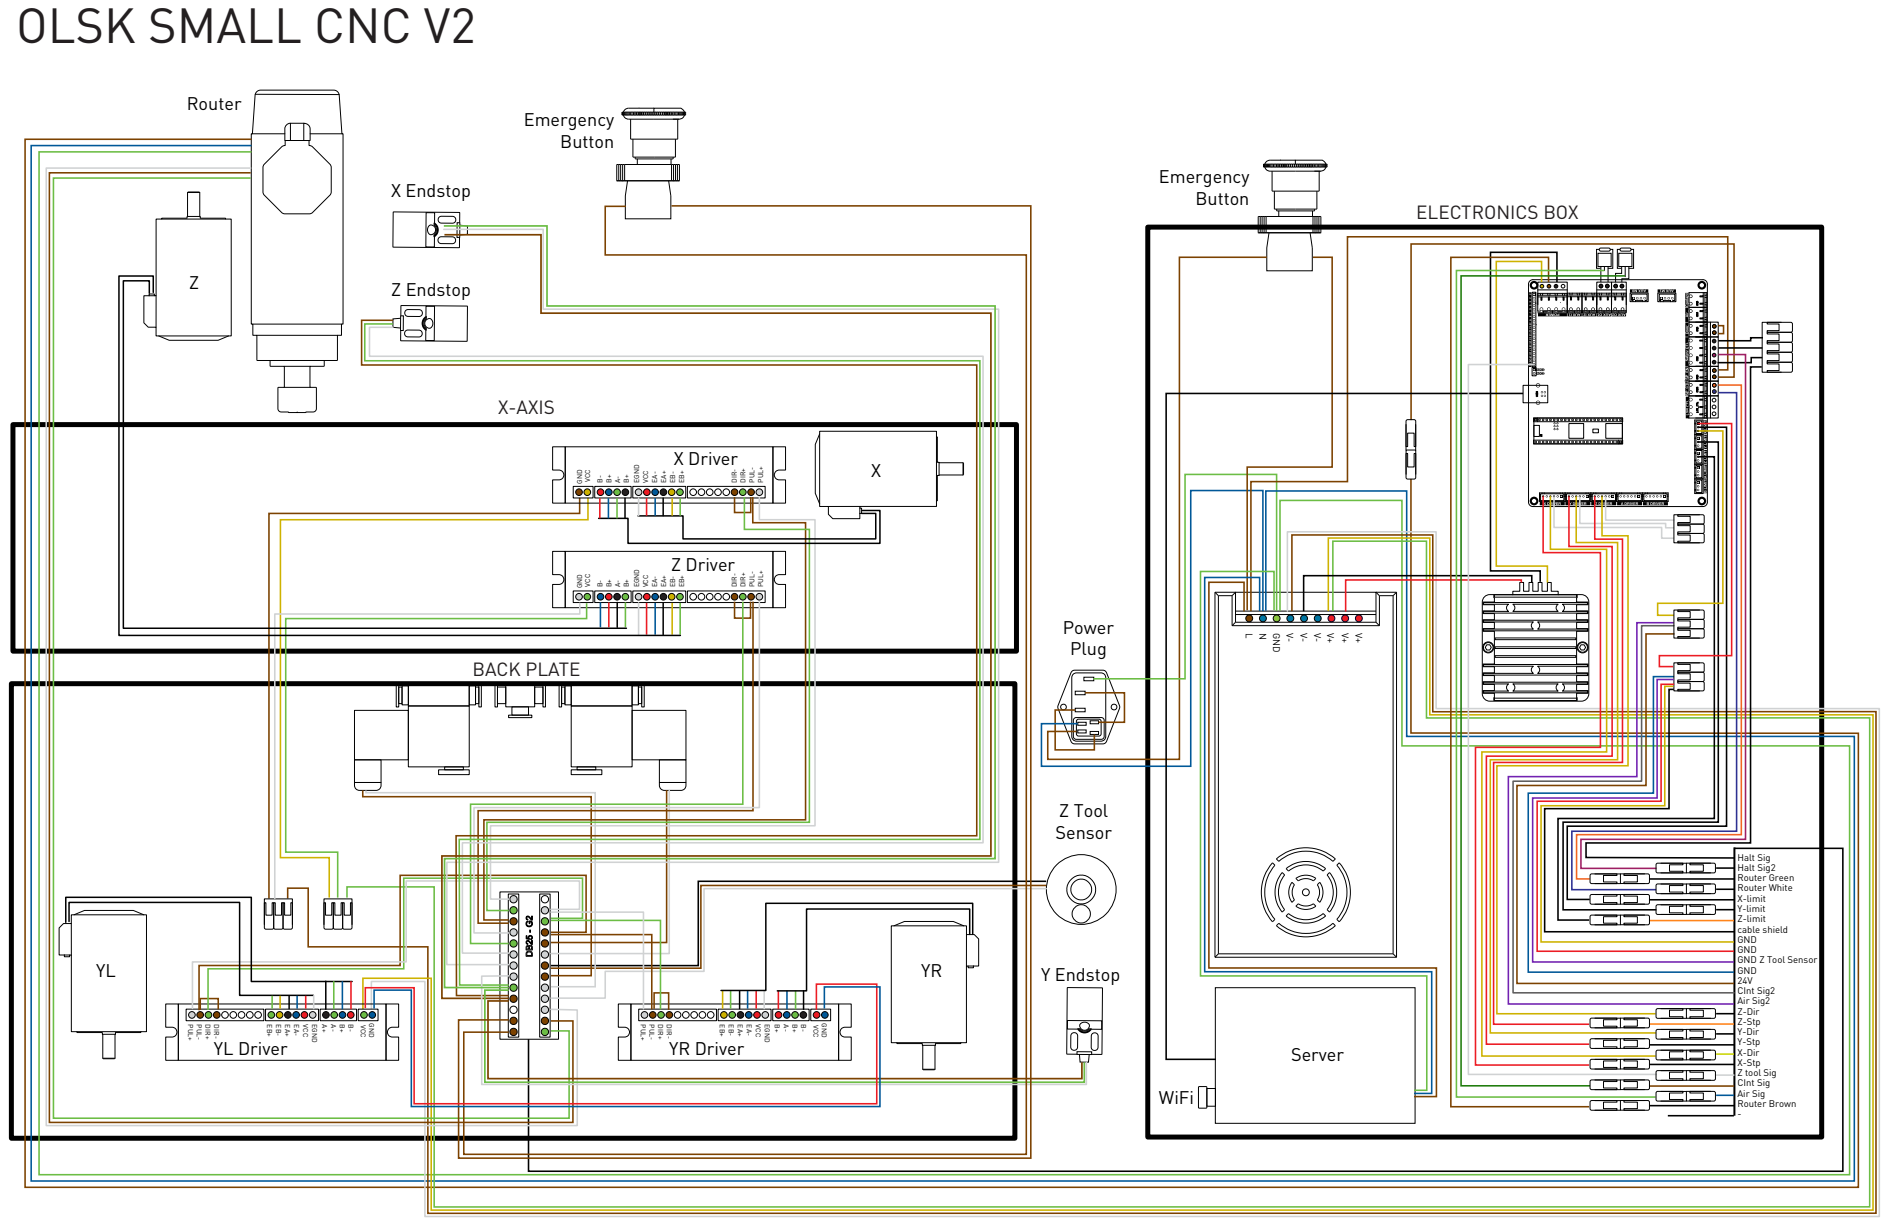
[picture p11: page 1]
GND; CInt Sig; CInt Sig2; X-Stp; X-Dir; Y-Stp; Y-Dir; Z-Stp; Z-Dir; Air Sig2; Z-limit; Y-limit; X-limit; Halt Sig2 Router Green Router White; cable shield GND GND GND Z Tool Sensor; Router Brown -; Z tool Sig; Halt Sig; Air Sig; VCC; EGND; DIR-; DIR+; PUL-; PUL+; Y Endstop; Server; WiFi; Z Tool Sensor; Power Plug; X Driver; Z Driver; YL Driver; YR Driver; X Endstop; Router; Emergency Button; ELECTRONICS BOX; X-AXIS; BACK PLATE

OLSK SMALL CNC V2

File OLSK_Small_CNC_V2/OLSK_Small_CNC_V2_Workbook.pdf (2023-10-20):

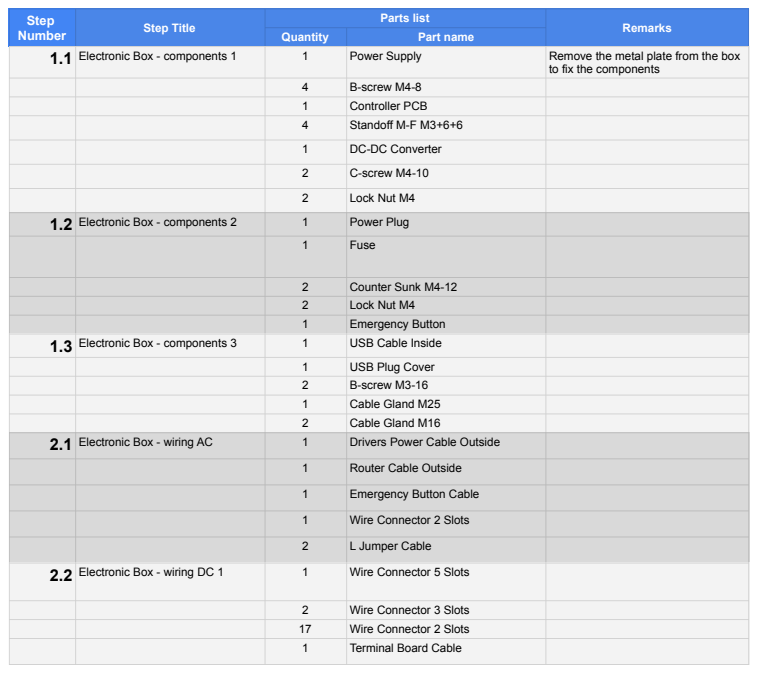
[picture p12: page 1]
Step; Number; Step Title; Parts list; Remarks; Quantity; Part name; 1.1 Electronic Box - components 1; Power Supply; Remove the metal plate from the box; B-screw M4-8; Controller PCB; Standoff M-F M3+6+6; DC-DC Converter; C-screw M4-10; Lock Nut M4; 1.2 Electronic Box - components 2; Power Plug; Fuse; Counter Sunk M4-12; Emergency Button; 1.3 Electronic Box - components 3; USB Cable Inside; USB Plug Cover; B-screw M3-16; Cable Gland M25; Cable Gland M16; 2.1 Electronic Box - wiring AC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

to fix the components

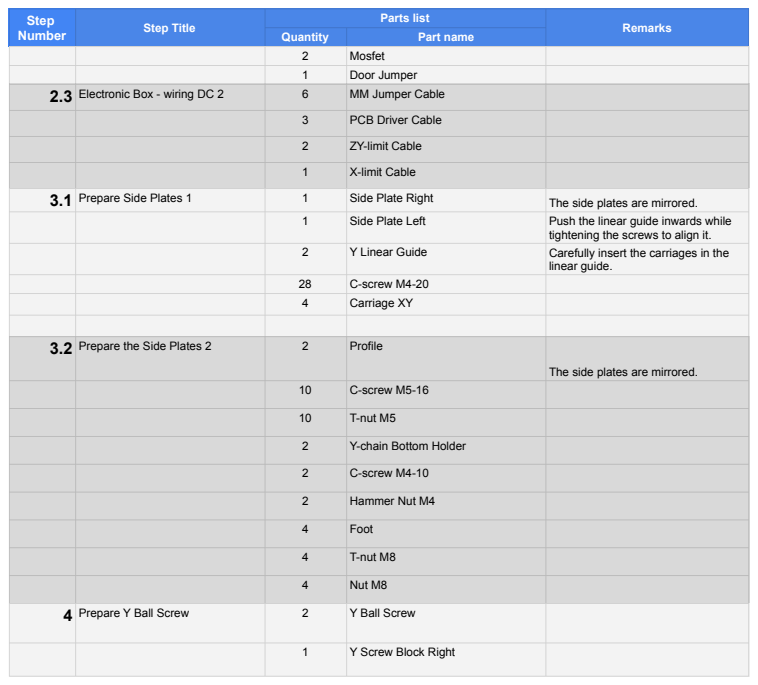
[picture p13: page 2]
Mosfet; Door Jumper; 2.3 Electronic Box - wiring DC 2; MM Jumper Cable; PCB Driver Cable; ZY-limit Cable; X-limit Cable; 3.1 Prepare Side Plates 1; Side Plate Right; The side plates are mirrored.; Side Plate Left; Push the linear guide inwards while; Y Linear Guide; Carefully insert the carriages in the; linear guide.; C-screw M4-20; Carriage XY; 3.2 Prepare the Side Plates 2; Profile; C-screw M5-16; T-nut M5; Y-chain Bottom Holder; C-screw M4-10; Hammer Nut M4; Foot; T-nut M8; Nut M8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

Step Number | Step Title | Parts list | Remarks

Quantity | Part name

tightening the screws to align it.

The side plates are mirrored.

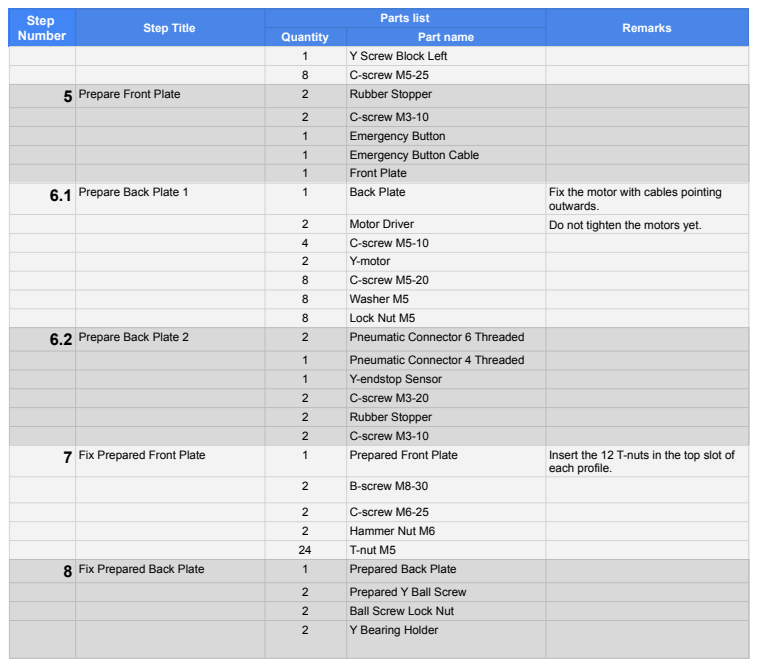
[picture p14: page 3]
Y Screw Block Left; C-screw M5-25; 5 Prepare Front Plate; Rubber Stopper; C-screw M3-10; Emergency Button; Emergency Button Cable; Front Plate; 6.1 Prepare Back Plate 1; Back Plate; Fix the motor with cables pointing; outwards.; Motor Driver; Do not tighten the motors yet.; C-screw M5-10; Y-motor; C-screw M5-20; Washer M5; Lock Nut M5; 6.2 Prepare Back Plate 2; Pneumatic Connector 6 Threaded; Pneumatic Connector 4 Threaded; Y-endstop Sensor; C-screw M3-20; 7 Fix Prepared Front Plate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

Step Number | Step Title | Parts list | Remarks

Quantity | Part name

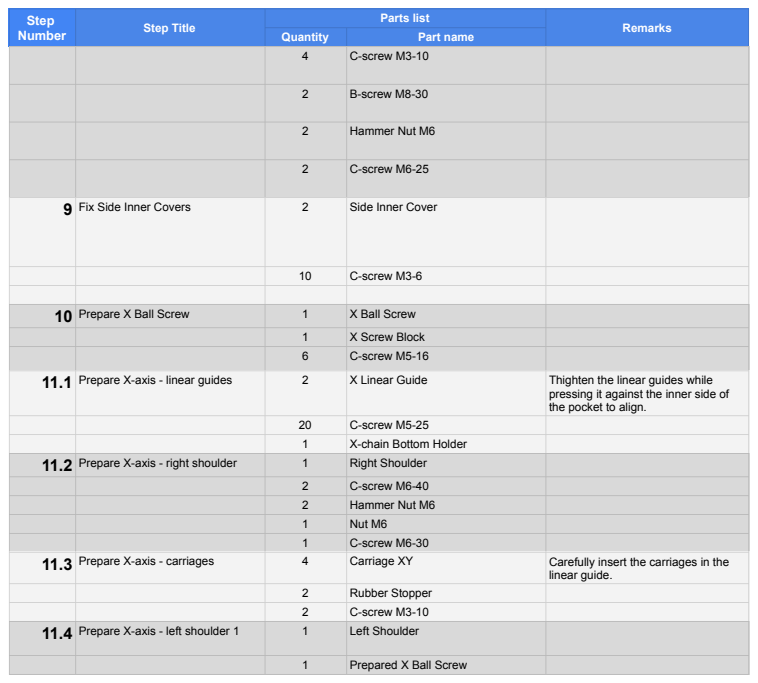
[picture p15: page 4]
C-screw M3-10; B-screw M8-30; Hammer Nut M6; C-screw M6-25; 9 Fix Side Inner Covers; Side Inner Cover; C-screw M3-6; 10 Prepare X Ball Screw; X Ball Screw; X Screw Block; C-screw M5-16; 11.1 Prepare X-axis - linear guides; X Linear Guide; Thighten the linear guides while; C-screw M5-25; X-chain Bottom Holder; 11.2 Prepare X-axis - right shoulder; Right Shoulder; C-screw M6-40; Nut M6; C-screw M6-30; 11.3 Prepare X-axis - carriages; Carriage XY; Carefully insert the carriages in the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

Step Number | Step Title | Parts list | Remarks

Quantity | Part name

pressing it against the inner side of
the pocket to align.

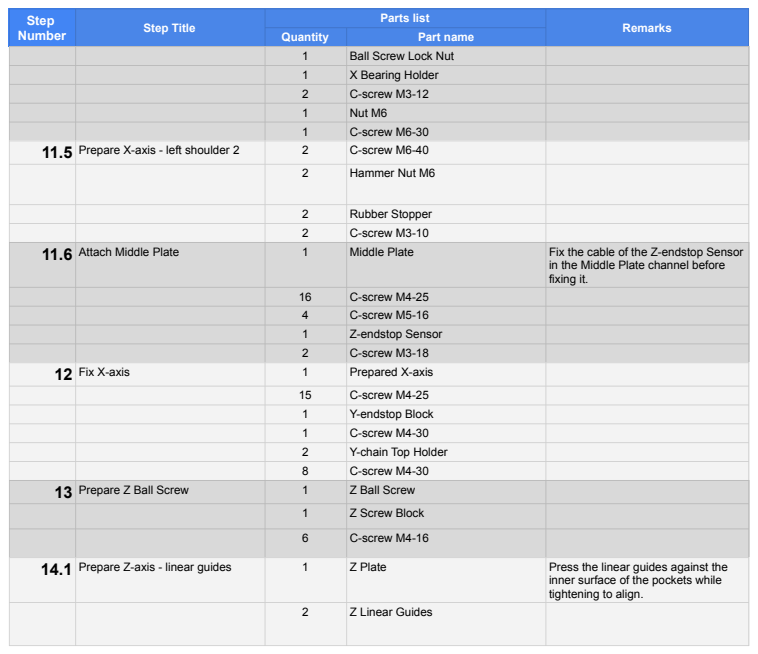
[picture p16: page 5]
Ball Screw Lock Nut; X Bearing Holder; C-screw M3-12; Nut M6; C-screw M6-30; 11.5 Prepare X-axis - left shoulder 2; C-screw M6-40; Hammer Nut M6; Rubber Stopper; C-screw M3-10; 11.6 Attach Middle Plate; Middle Plate; Fix the cable of the Z-endstop Sensor; C-screw M4-25; C-screw M5-16; Z-endstop Sensor; C-screw M3-18; 12 Fix X-axis; Prepared X-axis; Y-endstop Block; C-screw M4-30; Y-chain Top Holder; 13 Prepare Z Ball Screw; Z Ball Screw; Z Screw Block; C-screw M4-16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

Step Number | Step Title | Parts list | Remarks

Quantity | Part name

in the Middle Plate channel before
fixing it.

inner surface of the pockets while
tightening to align.

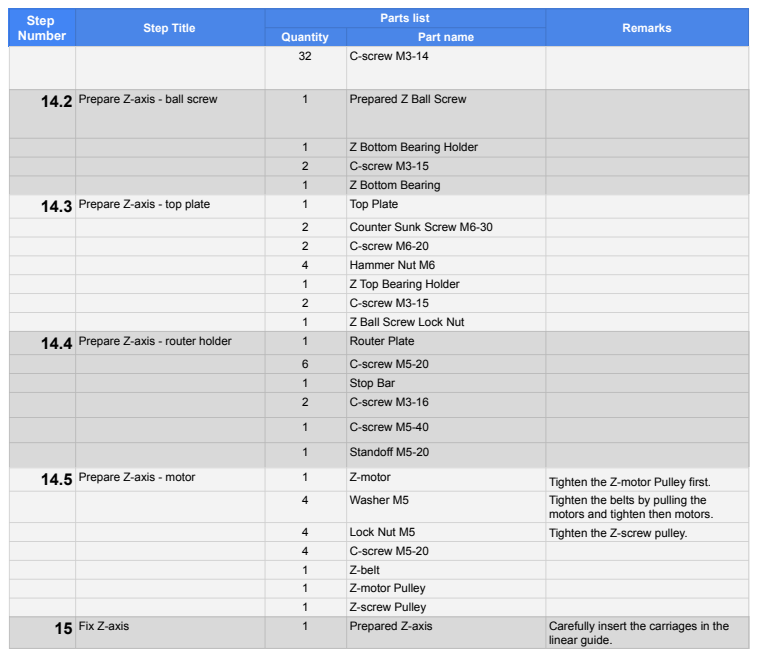
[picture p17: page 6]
C-screw M3-14; 14.2 Prepare Z-axis - ball screw; Prepared Z Ball Screw; Z Bottom Bearing Holder; C-screw M3-15; Z Bottom Bearing; 14.3 Prepare Z-axis - top plate; Top Plate; Counter Sunk Screw M6-30; C-screw M6-20; Hammer Nut M6; Z Top Bearing Holder; Z Ball Screw Lock Nut; 14.4 Prepare Z-axis - router holder; Router Plate; C-screw M5-20; Stop Bar; C-screw M3-16; C-screw M5-40; Standoff M5-20; 14.5 Prepare Z-axis - motor; Z-motor; Tighten the Z-motor Pulley first.; Washer M5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

Step Number | Step Title | Parts list | Remarks

Quantity | Part name

motors and tighten then motors.

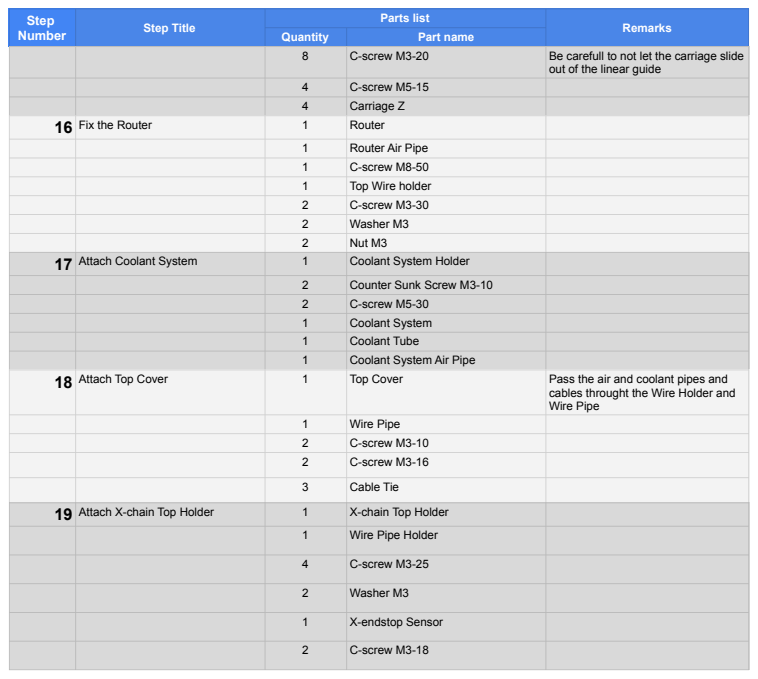
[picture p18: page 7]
C-screw M3-20; Be carefull to not let the carriage slide; C-screw M5-15; Carriage Z; 16 Fix the Router; Router; Router Air Pipe; C-screw M8-50; Top Wire holder; C-screw M3-30; Washer M3; Nut M3; 17 Attach Coolant System; Coolant System Holder; Counter Sunk Screw M3-10; C-screw M5-30; Coolant System; Coolant Tube; Coolant System Air Pipe; 18 Attach Top Cover; Top Cover; Pass the air and coolant pipes and; Wire Pipe; C-screw M3-10; C-screw M3-16; Cable Tie; 19 Attach X-chain Top Holder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

Step Number | Step Title | Parts list | Remarks

Quantity | Part name

out of the linear guide

cables throught the Wire Holder and
Wire Pipe
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

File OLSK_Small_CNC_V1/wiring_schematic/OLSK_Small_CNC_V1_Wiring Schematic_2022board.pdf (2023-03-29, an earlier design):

# USB

# OLSK SMALL CNC V1

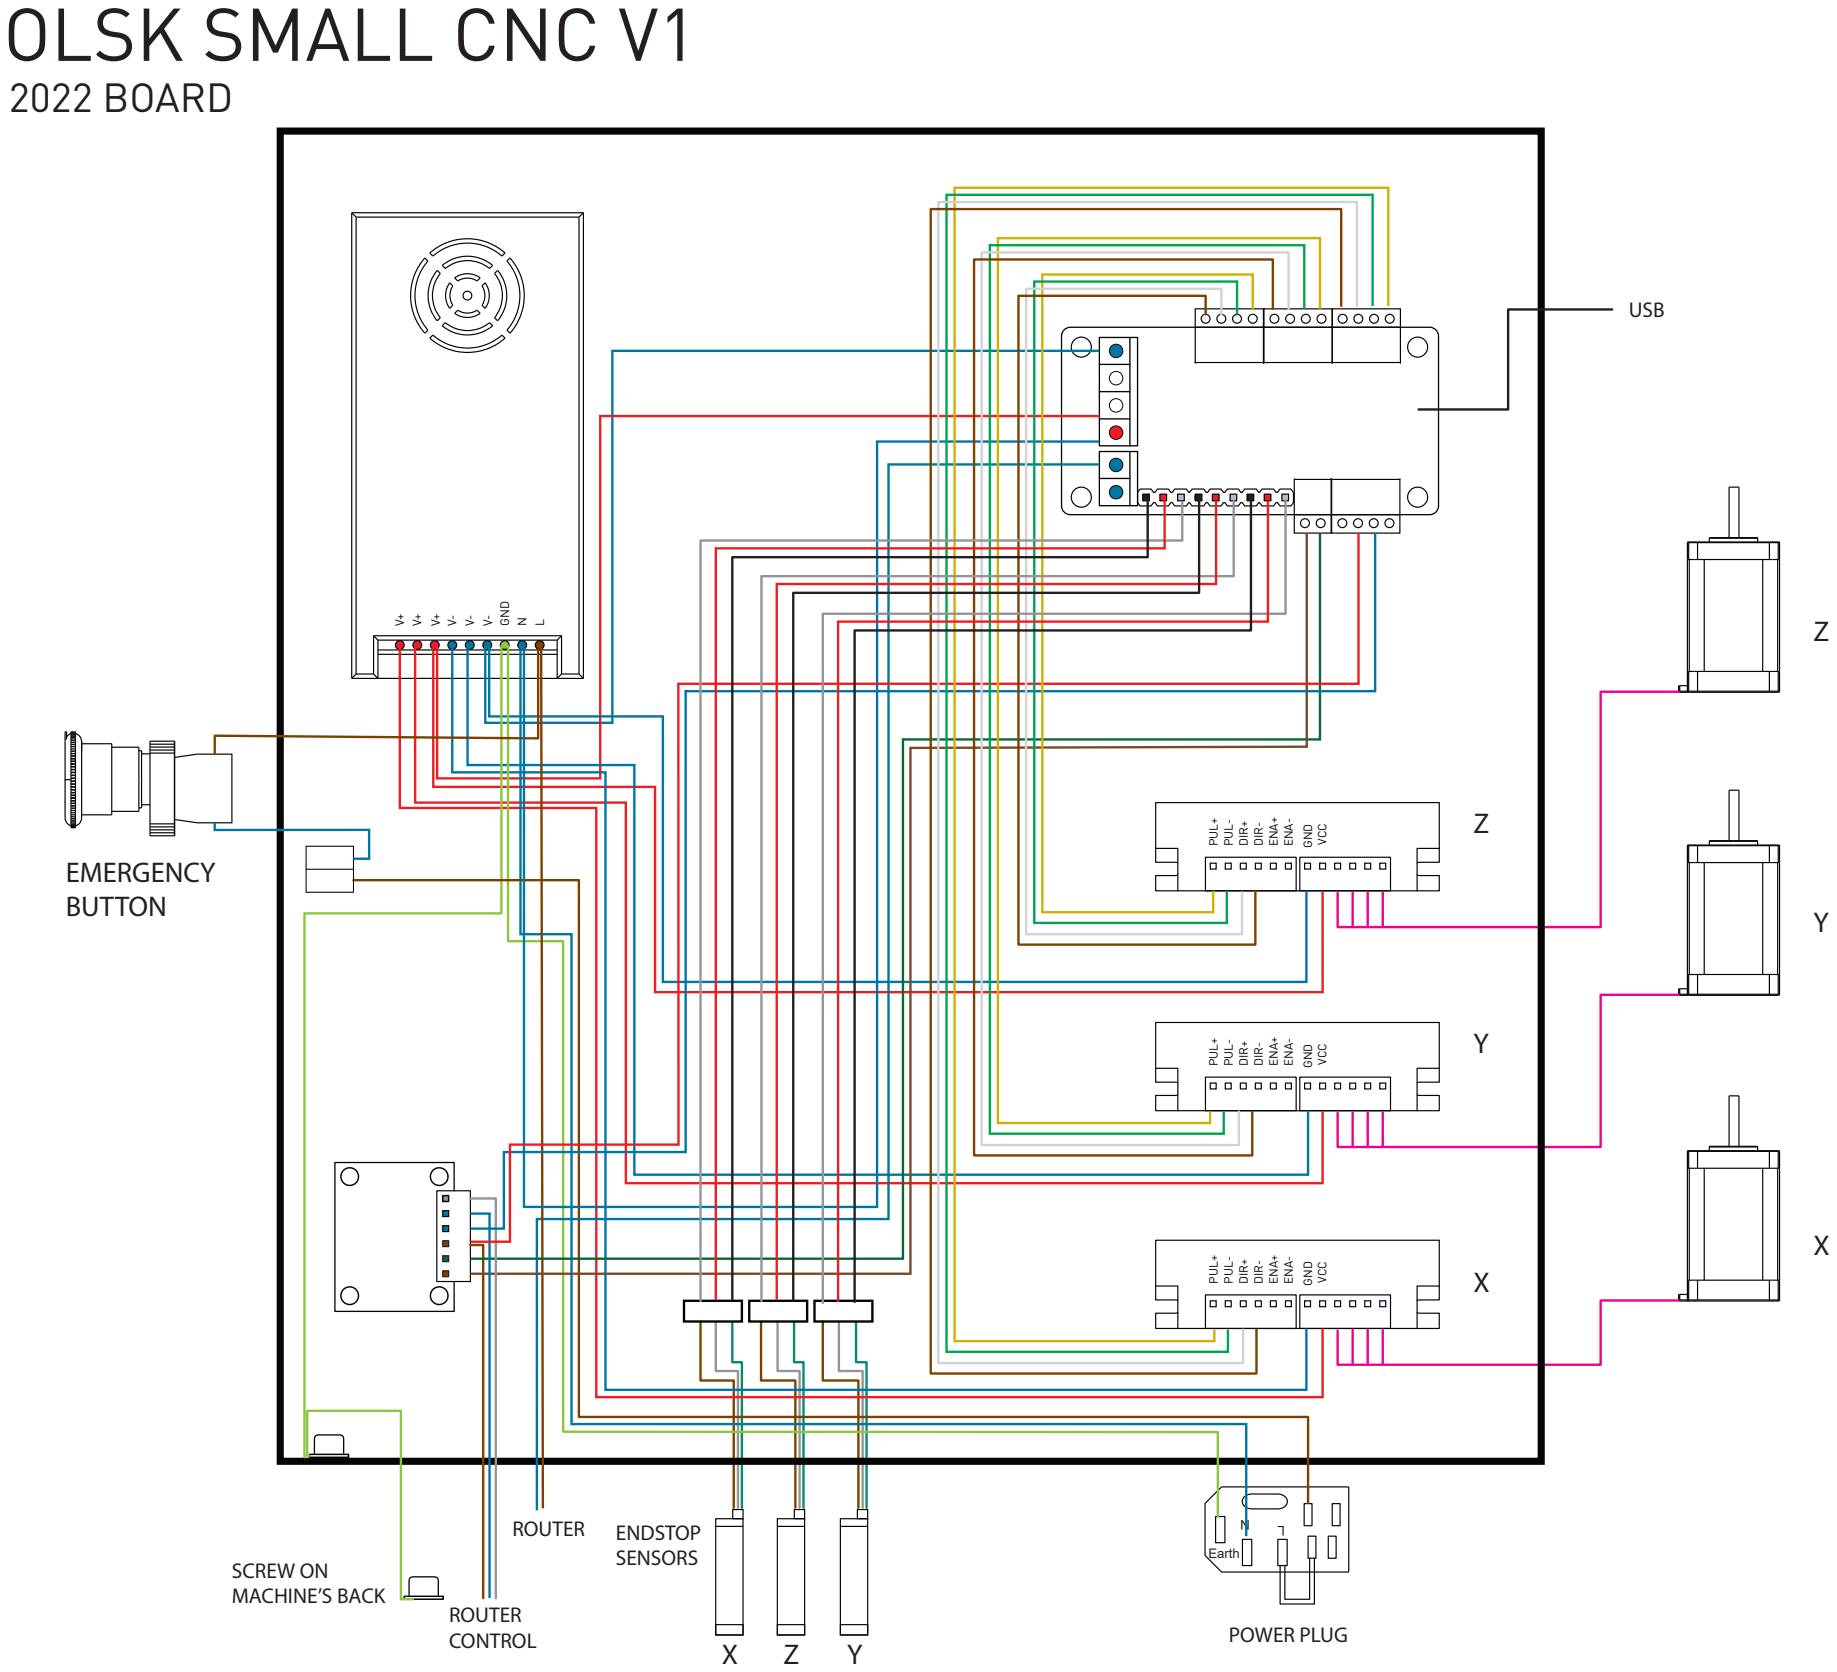
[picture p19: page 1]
GND; VCC; SCREW ON MACHINE’S BACK; EMERGENCY BUTTON; POWER PLUG; ENDSTOP SENSORS; ROUTER CONTROL; ROUTER; PUL+ PUL- DIR+ DIR-; ENA+ ENA-; Earth; 2022 BOARD

PUL+ PUL- DIR+ DIR- ENA+ ENA-

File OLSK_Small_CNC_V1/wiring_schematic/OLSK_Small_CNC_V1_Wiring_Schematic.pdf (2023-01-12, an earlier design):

# USB

# OLSK SMALL CNC V1

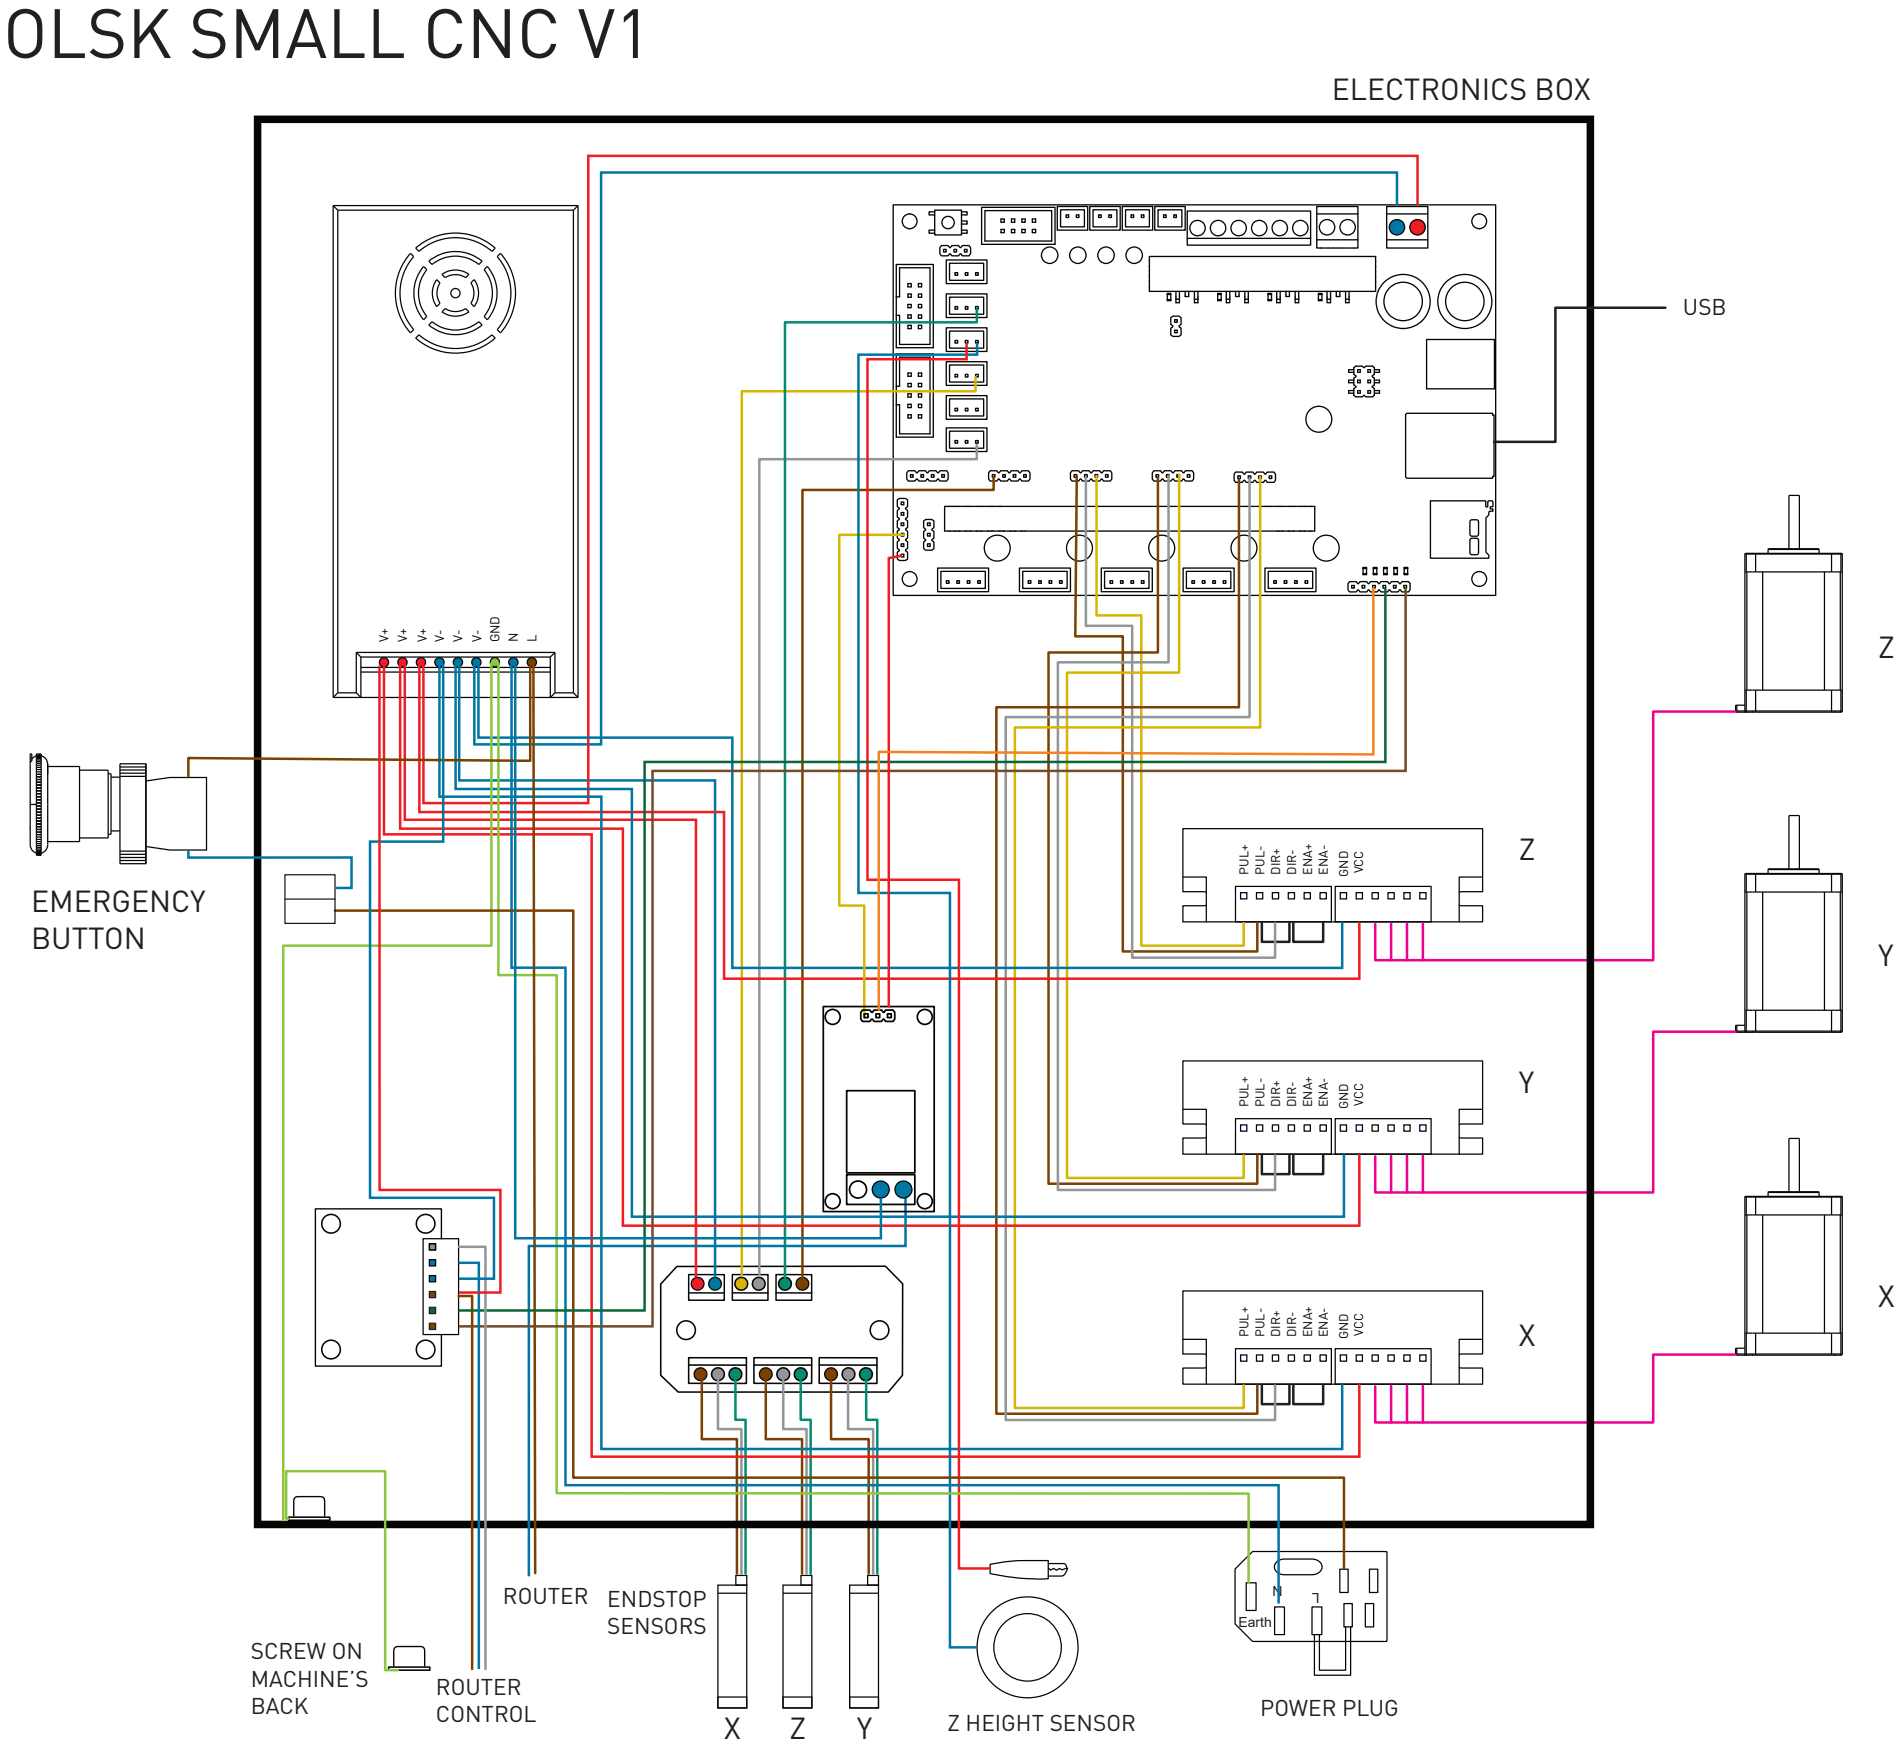
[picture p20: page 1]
GND; VCC; SCREW ON MACHINE’S BACK; EMERGENCY BUTTON; ENDSTOP SENSORS; ROUTER CONTROL; ROUTER; PUL+ PUL- DIR+ DIR-; ENA+ ENA-; Earth; ELECTRONICS BOX

PUL+ PUL- DIR+ DIR- ENA+ ENA-

POWER PLUG Z HEIGHT SENSOR

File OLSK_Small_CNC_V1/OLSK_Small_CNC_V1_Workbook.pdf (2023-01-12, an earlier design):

## Step

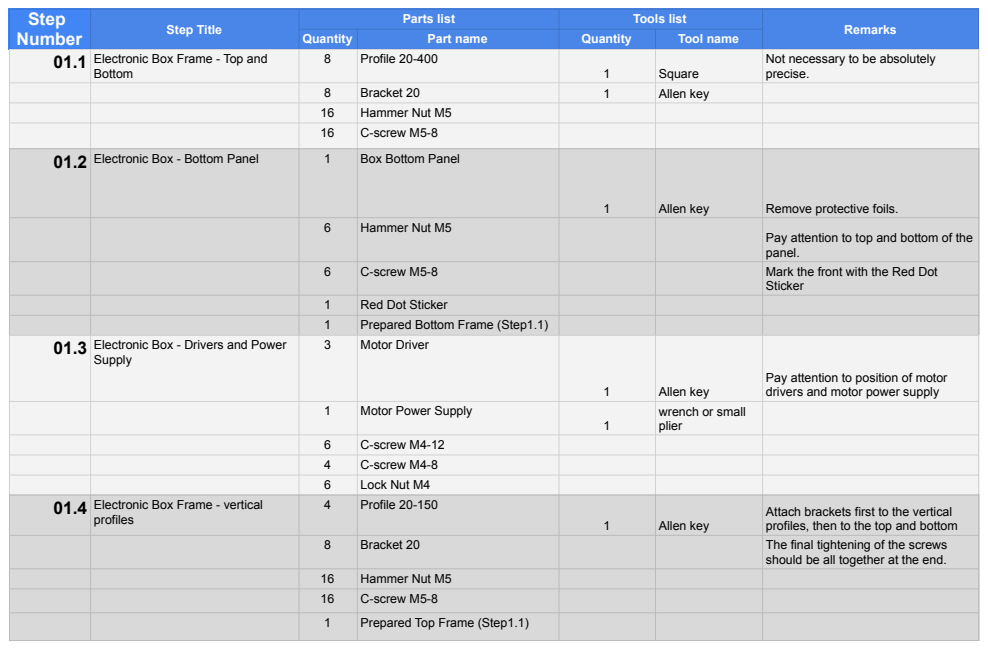
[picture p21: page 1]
Number; Step Title; Parts list; Tools list; Remarks; Quantity; Part name; Tool name; Bottom; Profile 20-400; Square; Bracket 20; Allen key; Hammer Nut M5; C-screw M5-8; 01.2 Electronic Box - Bottom Panel; Box Bottom Panel; Remove protective foils.; Mark the front with the Red Dot; Sticker; Red Dot Sticker; Prepared Bottom Frame (Step1.1); Supply; Motor Driver; Motor Power Supply; C-screw M4-12; C-screw M4-8; Lock Nut M4; profiles; Profile 20-150; The final tightening of the screws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

01.1 Electronic Box Frame - Top and

Not necessary to be absolutely
precise.

Pay attention to top and bottom of the
panel.

01.3 Electronic Box - Drivers and Power

Pay attention to position of motor
drivers and motor power supply

wrench or small
plier

01.4 Electronic Box Frame - vertical

Attach brackets first to the vertical
profiles, then to the top and bottom

should be all together at the end.

Step Number | Step Title | Parts list | Tools list | Remarks

01.5 Electronic Box - PCBs; Standoff; Small screwdriver Phillips; Controller PCB; Allen Key; Plastic Screw M3-8; Router PCB; Relay; Sensor PCB; 02.1 Prepare Left Panel; USB Cable Inside; Small screwdriver; Phillips; Remove protective foil from panel; Box Left Panel; 02.2 Prepare Back Panel; Box Back Panel; Allen key; Cable Gland; Power Socket + Mains Cable; C-screw M3-10; Lock Nut M3; Washer M3; Panels; Prepared Left Panel (Step 2); Remove protective foil from panels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

Quantity | Part name | Quantity | Tool name

Wrench or small
plier

02.3 Attaching Sides, Front and Back

Step Number | Step Title | Parts list | Tools list | Remarks

03.1 Preparing Ball Screw Y; C-screw M5-16; Allen key; Ball Screw Y; Screw Block Y; 03.2 Preparing Ball Screw X; Ball Screw X; Screw Block X; 03.3 Preparing Ball Screw Z; C-screw M4-16; Ball Screw Z; Screw Block Z; 04.1 Preparing the Y-axis - linear guides; Linear Guide Y; Arrows should be pointing outside; Base Plate; Flip the base upsidedown; Push the linear guides outwards to; align.; 04.2 Preparing the Y-axis - Carriages; Carriage; Insert the carriages to the same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

Quantity | Part name | Quantity | Tool name

direction as the writings of the linear
guide.

Step Number | Step Title | Parts list | Tools list | Remarks

04.5 Attaching Y Back Bearing Holder; Prepared Ball Screw Y; Rubber Hammer; C-screw M8-30; Allen key; Y Back Bearing Holder; Wrench; Locknut pitch1mm; Washer M12; 05.1 Completing the base - Back; Base back; C-screw M5-20; C-screw M5-25; Wire Fixer Small; Air Splitter Holder; 05.2 Completing the base - Profiles; Profile 40-800; C-screw M8-25; T-nut 8 M6; C-screw M6-16; Washer M8 Big; support; Shoulder Support Left; Shoulder Support Right; Shoulder Support Connector; C-screw M5-16; C-screw M4-30

Quantity | Part name | Quantity | Tool name

Insert the Ball Screw Y in the Y Back
Bearing in the right direction.
Insert the other end of the Ball Screw
Y in the Y Front Bearing with a rubber
hammer.

The Ball Spindle Y housing should
have the filleted side facing the Base
Plate

Make sure to align the T-nuts to the
Base Plate holes

05.3 Completing the base - shoulders

Step Number | Step Title | Parts list | Tools list | Remarks
Quantity | Part name | Quantity | Tool name
| 4 | C-screw M8-25
05.4 Attaching the bed to the base | 12 | B-screw M6-20
1 | Allen key | Flip the Base Plate.
| 1 | Bed
06.1 Preparing the X-axis - linear guides | 2 | Linear Guide X
| | | 1 | Allen key

All arrows of the linear guides should be pointing down.
1 | X-axis Plate | To ensure a good alignment, force
the linear guide inwards while tightening the screws
| 20 | C-screw M4-16
06.2 Preparing the X-axis - carriages | 4 | Carriage | Insert the carriages to the same
direction as the writings of the linear guide.
06.3 Attaching the X-axis - left shoulder | 1 | Left Shoulder | 1 | Allen key
| 6 | C-screw M8-40
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

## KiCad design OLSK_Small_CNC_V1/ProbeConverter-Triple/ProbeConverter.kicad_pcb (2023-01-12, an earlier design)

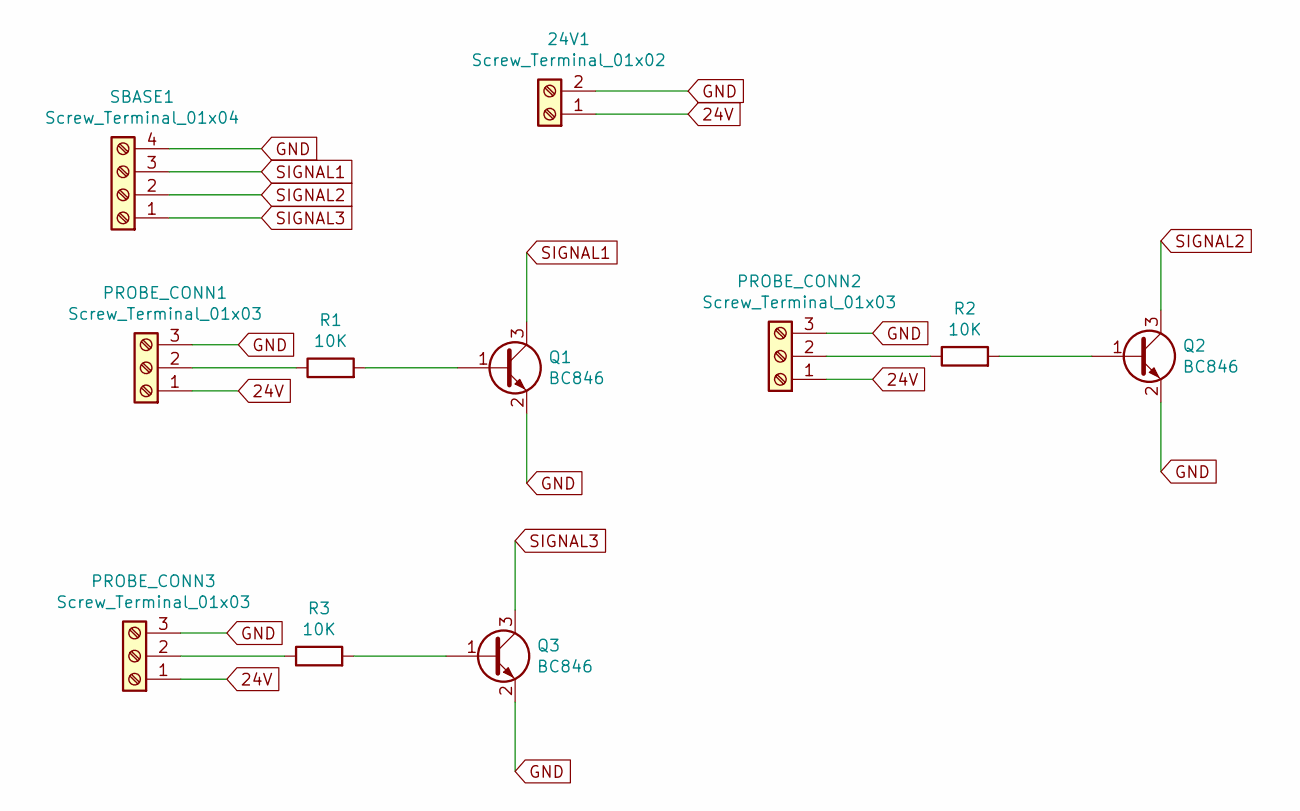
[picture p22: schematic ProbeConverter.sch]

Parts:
24V1: Screw_Terminal_01x02; TerminalBlock_bornier-2_P5.08mm
PROBE_CONN1, PROBE_CONN2, PROBE_CONN3: Screw_Terminal_01x03; TerminalBlock_bornier-3_P5.08mm
Q1, Q2, Q3: BC846; SOT-23
R1, R2, R3: 10K; R_1206
SBASE1: Screw_Terminal_01x04; TerminalBlock_bornier-4_P5.08mm

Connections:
24V: 24V1.1, PROBE_CONN1.1, PROBE_CONN2.1, PROBE_CONN3.1
GND: 24V1.2, PROBE_CONN1.3, PROBE_CONN2.3, PROBE_CONN3.3, Q1.2 (E), Q2.2 (E), Q3.2 (E), SBASE1.4
unnamed: PROBE_CONN1.2, R1.1
unnamed: PROBE_CONN2.2, R2.1
unnamed: PROBE_CONN3.2, R3.1
unnamed: Q1.1 (B), R1.2
unnamed: Q2.1 (B), R2.2
unnamed: Q3.1 (B), R3.2
SIGNAL1: Q1.3 (C), SBASE1.3
SIGNAL2: Q2.3 (C), SBASE1.2
SIGNAL3: Q3.3 (C), SBASE1.1

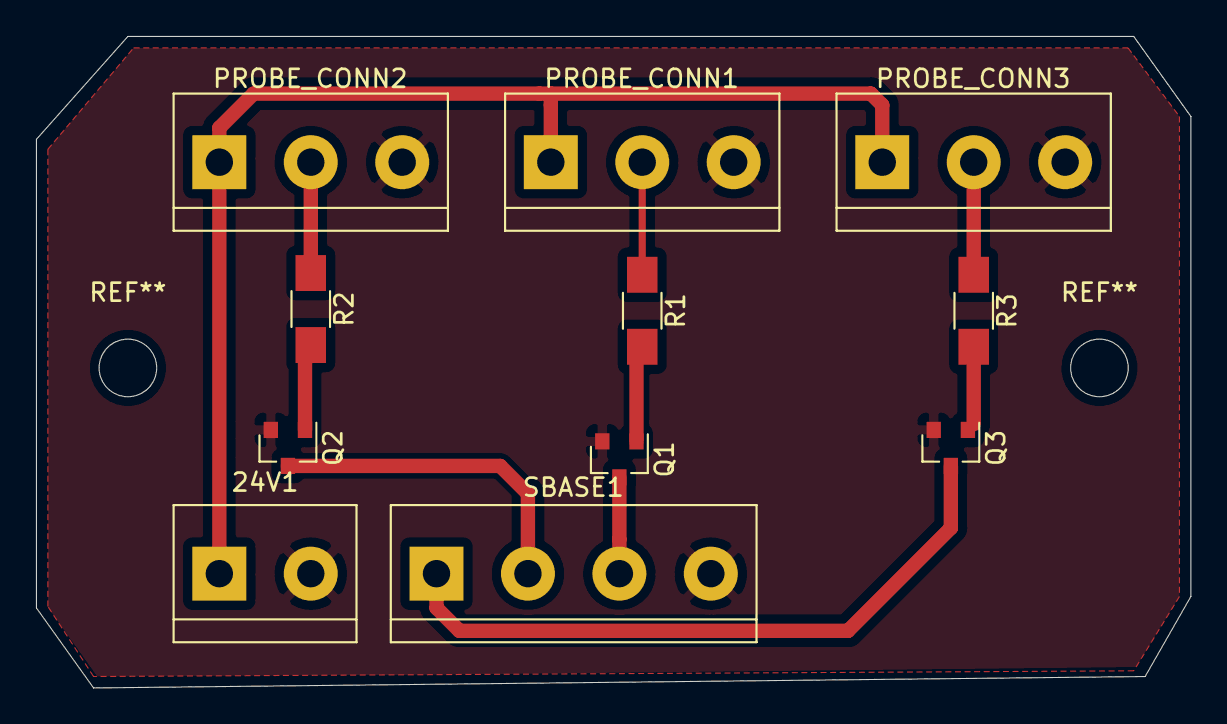
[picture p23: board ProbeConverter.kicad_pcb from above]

Board: 2 copper layers, 64.1 x 36.2 mm, 11 parts (0 on the bottom side), 11 nets.

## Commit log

2022-12-24 added picture, specs and CAD files
2023-01-12 Update README.md
    added firmware and pcb
2023-01-12 upload pcb anf firmware files
    [ProbeConverter.kicad_pcb, ProbeConverter.sch]
2023-01-12 upload workbook and wiring schematic
2023-01-12 upload BOM
2023-01-12 Update README.md
    added bom, workbook and wiring schematic
2023-01-12 fix wiring schematic file name
2023-03-29 upload z tool probe
2023-03-29 upload versions of wiring
2023-03-29 Update README.md
    update wiring schematic link
2023-10-20 Create V1 Folder
    [ProbeConverter.kicad_pcb, ProbeConverter.sch]
2023-10-20 add CAD
2024-03-05 update wiring
2024-10-06 added CAD for workshop, Fusion 360 version
2024-10-06 added CAD for workshop, step version
2025-03-11 Upload Assembly Manual
2025-03-13 Update Assembly Manual
2025-03-13 Update V3
    [Small CNC V3 Tools Positions_.xlsx]
2025-03-13 Upload cad
